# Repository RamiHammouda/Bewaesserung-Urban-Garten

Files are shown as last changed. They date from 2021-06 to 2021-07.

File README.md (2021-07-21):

# Bewaesserung Urban Garden

**HTW Smart Garden Watering System** is **_InternetOfThing_** **(IoT)**  **LoraWan** based Project from a wonderful suggestion of Mr. Prof. Dr.-Ing. Mohammad Abuosba. The target of the project is to build a smart watering system for an urban garden in HTW Berlin. 
<br/> <br/>
# Motivation
The ca.800m<sup>2</sup> Urban garden in HTW Berlin locates in the back of the university, next to the famous Spree River. It is a really beautiful garden which provides everyone fresh air along with really wonderful green feeling due to many trees and plants. And to have more time to enjoy it or to keep this feeling lasts forever, a smart watering system comes up as an answer :). 
<br/> <br/>
# Screenshot

 UI Program

# Usage

# Technology stack:
#### Operation System:
- Windows 10/(Linux)
#### IDE:
- Visual Studio Code
- Platform IO
#### Frameworks:
- Arduino
#### Dependencies:
- MCCI LoraWAN LMIC Library v4.4
- Adafruit Unified Sensor v1.1.4
- Adafruit BME280 v2.1.4
- Thingpulse/ESP8266 and ESP32 OLED driver for SSD1306 displays v4.2.0 (platformio lib install 2978)
- ~~NewPing v1.9.1~~ (replaced with our own implemented class)
#### Protocol:
- MQTT, HTTP
#### Connectivity Protocol:
- LoRaWAN (Long Range Wide Area Network)
#### Tools:
- MQTT Mosquito
- MQTT Explorer
- MQTT Fx
#### Server:
- TTN (thethingsnetwork)
#### UI Programming: 
- JavaScript
- Node-Red Framework
#### UI Dependencies:
- node-red-dashboard (base)
- node-red-contrib-ui-led (led only)
- node-red-contrib-telegrambot (connect to telegram bot API)
- node-red-contrib-remote (remote system on Mobile)
#### Hardware Programming: 
- C++
#### Hardware:
- Lora32 (TTGO-Lora v2.1.6)
+ BME280 Sensor
+ YF-S201 Waterflow sensor
+ Water pressure sensor 
+ HC-SR04 Ultrasonic sensor
+ Capacitive soil moisture sensor v1.2
+ Water pump
+ Magnetic Ventil
+ SRD-05VDC-SL-C 4 CH Relay
<br/> <br/>
# Feature List

##### Controlling Sensors, Actors:
- [x] Collect current ambient parameters (Temperatur sensor, Humidity sensor, Air pressure sensor.. )
- [x] Collect current water level in water tank (Ultrasound sensor)
- [x] Collect current water hose parameters (Water pressure sensor, Water flow sensor)
- [x] Control Actors (Water pump, Magnetic valve)
##### On LoraWan Server:
- [x] Send collected sensor data to TTN Network
- [x] Operate with ABP Mode or OTAA Mode (prefer OTAA)
- [x] Support float decode payload
- [x] Support int decode payload
- [x] Binding Server with opensensemap.org
##### Operate Actors:
- [x] Watering System can run independently of controlling UI
- [x] Actors can be manually remote-controlled 
- [x] Actors can operate itself automatically based on pre-configuration
     - [x] Watering will turn on if Moisture (Dryness) Value over a definied value (default is 95%)
     - [x] Watering will turn off if Moisture (Dryness) Value under a definied value (default is 90%)
     - [x] Watering will turn off if Water Level under a definied value (default is 10%)
     - [x] Watering will turn off if Waterflow Volume over a definied value (default is 10L for testing)(experiment feature)
- [x] Auto Mode and Manual Mode should be selectable (by Master Switch)
- [x] Remote control actors manually 
- [x] Updating-sensor Tempo is changeable (through Debug Mode on/off for quick/slow)
##### Sensor Data Visualization:
- [x] Simple sensor data are visualizated by opensensemap
- [x] Complex sensor data will be visualizated by a self development UI
##### UI Development:
- [x] Create an UI to get all current information of system ( Temperatur, Humidity, Moisture Value, Air Pressure, Water Pressure, Waterflow Speed, Waterflow Volume, current status of Ventil, current status of Pump, current Update Tempo, current operation status of system)
- [x] Assisten Management Information (Streng of Signal, Noise Ratio, relative Water Pressure, Curent Operation Mode )
- [x] Control actors through simple user-friendly UI like button, not on JSON UI 
      (comply to requirement from Mr. Prof. Dr.-Ing. Abuosba )
- [x] Pre-configuration parameters should be changeable (e.g through input fields) 
      (comply to suggestion from Mr. Holger Martin )
##### Options:
- [x] An UI on mobile for convenient monitoring
- [x] Send Notification to user for alert and notify current status automatically through Telegram with Bot "HTWGarden". (Only Admin received alert)
- [x] Everyone can query current important status of system through Telegram bot "HTWGarden"
- [x] Create wrapper classes for multiple sensors/actors (for an easy scalability)
 <br/> <br/>
## For testing purpose
#### THETHINGSNETWORK.ORG _(Legacy V2 Console)_
- ##### User name: _htwgardenproject_
- ##### Email address: _htwgardenss21@gmail.com_
- ##### Password: _htwgarden2021_

## UI Rebuild: (build from Flow.json file)
**Default:**
- **Logic base: _localhost:1880_**
- **UI board: _localhost:1880/ui_**
### MQTT Topic Setting:
- **MQTT-In Topic:**  **_mygardenproject/devices/sensortest02/up_**
- **MQTT-Out Topic:**  **_mygardenproject/devices/sensortest02/down_**
- **Server:**  **_eu.thethings.network_**
- **Port:**  **_1883_**
- **Protocol:**  **_MQTT V3.1.1_**
- **Username:**  **_mygardenproject_**
- **Password:**  **_ttn-account-v2.60jnFj-pF6rapK8BtiWsr2CQXM8TufQspWzjreeI2Zc_**
### Telegrambot:
- **Bot-Name: _HTWGarden_**
- **Token: _1565148953:AAHQ8Jx3c4r1mIf3uV5PS_4BW0aKDrDjfuM_**
 <br/> <br/>
# License
**MIT** © **HTW Berlin - IngenieurInformatik SS21** - **Team 4 - Khac Hoa Le, Rami Hammouda, Jaro Machnow**

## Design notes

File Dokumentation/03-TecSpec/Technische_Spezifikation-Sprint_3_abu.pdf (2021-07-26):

Technische Spezifikation - Smarte Gartenbewässerung

# Technische Spezifikation

# Smarte Gartenbewässerung über LoRaWAN

Mitarbeiter und Autoren:

- Rami Hammouda
- Khac Hoa Le
- Jaro Machnow

Letzte Änderung: 21.07.2021

Version: 1.5

21.07.2021 | Seite 1 von 39

## eine insgesamt sehr gute technische Spezifikation. Die Pin-Belegung im Schaltplan

sowie die Bemaßung des Gehäuses für den Ultraschallsensor fehlen.
weitere kleine Anmerkungen siehe unten.

## Wertung: TechSpec : 5 Punkte Projektplan : 5 Punkte

Technische Spezifikation - Smarte Gartenbewässerung

Inhaltsverzeichnis

1. Einleitung | 4
1.1 Überblick | 4
1.2 Definitionen und Abkürzungen | 4
1.3 Vorhandene Dokumente | 4
2. Prozessüberblick | 4
2.1 Realisierungsprozess | 5
2.2 Fachlicher Workflow | 7
2.3 Checkliste | 8
3. Systemarchitektur und Infrastruktur | 10
3.1 Systemarchitektur | 10
3.2 Beschreibung der Komponenten | 11
4. Technische Spezifikation der Software | 12
4.1 Überblick Software-Komponenten | 12
4.2 Schnittstellen zwischen den Komponenten | 14
4.3 Technologiestack | 15
4.4 Anmeldedaten für TTN | 16
4.5 Erste Testphase - Senden und Empfangen von Daten über TTN | 17
4.6 Entwicklung der User Interface (UI) | 23
4.7 Integration von Telegram | 25
4.8 Lora32-Komponente: Klassendiagramm | 26
4.9 Autonome Steuerung | 27
4.10 Fehlererkennung und -behandlung | 29
5. Spezifikation der Hardware | 30
5.1 Einzelteile | 30
5.2 Schaltplan | 35
5.3 Halterung für den Ultraschallsensor | 37
5.4 Gesamtaufbau | 39

Technische Spezifikation - Smarte Gartenbewässerung

Versionshistorie

Version | Datum | Verantwortlich | Änderung
1.0 | 29.05.2021 | Jaro Machnow | Dokumenterstellung
1.1 | 06.06.2021 | Jaro, Hoa Le, Rami | Ergänzungen
1.2 | 15.06.2021 | Jaro, Hoa Le, Rami | Ergänzungen
1.3 | 16.06.2021 | Rami, Hoa, Jaro | Vervollständigung Sprint 1
1.4 | 15.07.2021 | Jaro, Hoa Le, Rami | Ergänzungen
1.5 | 21.07.2021 | Jaro, Hoa Le, Rami | Vervollständigungen Sprint 3

Technische Spezifikation - Smarte Gartenbewässerung

### 1. Einleitung

### 1.1 Überblick

Es wird eine smarte und möglichst preisgünstige und überwachte Bewässerung von Beeten per Netzwerksteuerung über das The-Things-Network (TTN) gebaut. Im Urban Garden kontrolliert ein Mikrocontroller entsprechend der über das Netzwerk gesendeten Nutzereingaben oder eines autonomen Workflows verschiedene Sensoren und Aktoren. Mit Hilfe einer LoRaWAN-Antenne werden die Daten der Sensoren vom Urban Garden aus in das Netzwerk gesendet und können auf einem entfernten Computer ausgelesen werden und als Visualisierung auf OpenSenseMap.org angesehen werden.

Zu den Mechanismen der autonomen Steuerung gehören vor allem das Abschalten des Wasserflusses im Falle eines Lecks und das eigenständige Starten der Bewässerung beim Erreichen einer bestimmten Bodenfeuchte.

Für alle eingebauten Komponenten und Funktionen gilt der Grundsatz, dass das System in Zukunft leicht modular erweitert werden kann.

### 1.2 Definitionen und Abkürzungen

LoRaWan -Long Range Wide Area Network TTN - The Things Network

### 1.3 Vorhandene Dokumente

Tabelle 1: Vohandene Dokumente

Dokument | Autor(en) | Datum
Lastenheft | Rami Hammouda, Khac Hoa Le, Jaro Machnow | 28.04.2021
Lastenheft + Kommentare | + Prof. Dr. Mohammad Abuosba | 30.04.2021
Anforderung-Email | Holger Martin | 10.04.2021
Pflichtenheft | Rami Hammouda, Khac Hoa Le, Jaro Machnow | 19.05.2021
Pflichtenheft + Kommentare | + Prof. Dr. Mohammad Abuosba | 25.05.2021

Technische Spezifikation - Smarte Gartenbewässerung

### 2. Prozessüberblick

### 2.1 Realisierungsprozess

Nachfolgend ist eine Darstellung aller Funktionen und deren Unterteilung im Projekt:

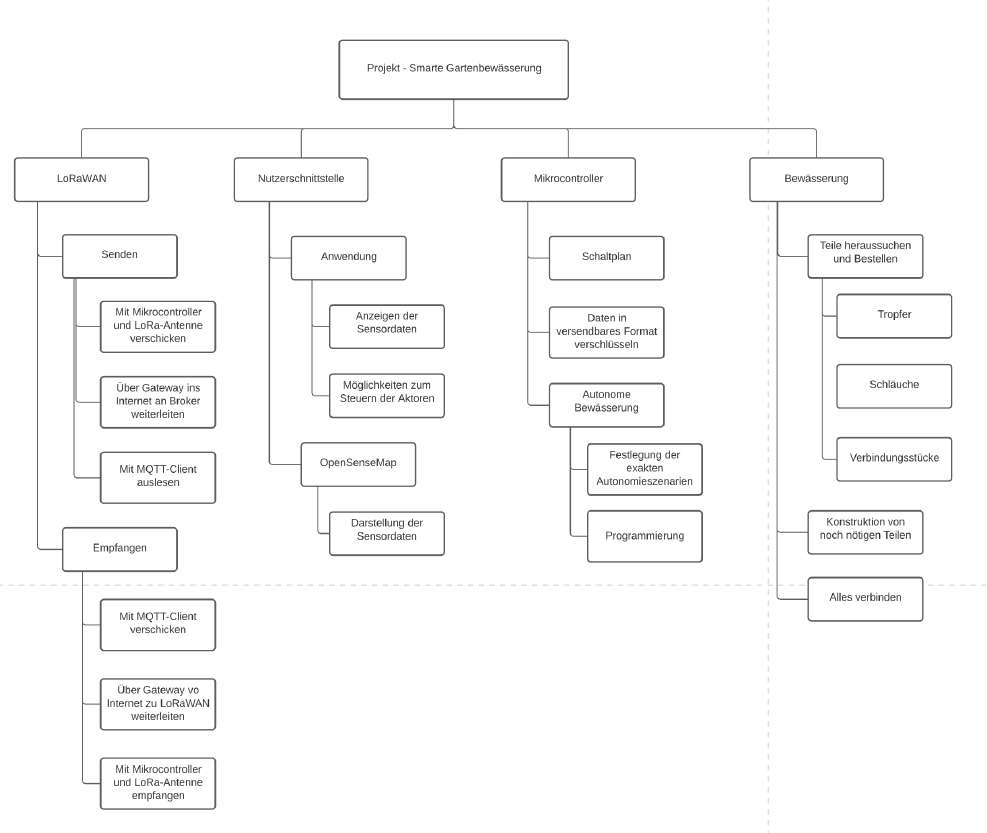
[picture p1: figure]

Abbildung 1: Übersicht über die Aufgabenstruktur

Für die Realisierung des Projektes ist es zuerst nötig, alle notwendigen Teile herauszusuchen und zu bestellen. Dann kann damit begonnen werden die Funktionsfähigkeit des Hauptziels des Projektes sicherzustellen: Das Senden und Empfangen von Daten vom Urban Garden über das LoRaWAN-Netzwerk. Danach können parallel die Nutzerschnittstellen mit TTN verbunden und programmiert werden und der Mikrocontroller mit den zugehörigen

Technische Spezifikation - Smarte Gartenbewässerung

Komponenten eingerichtet werden. Zum Schluss wird das gesamte Bewässerungssystem mit allen Komponenten zusammengebaut und im Urban Garden installiert.
Der Realisierungsprozess ist in folgendem Diagramm dargestellt:

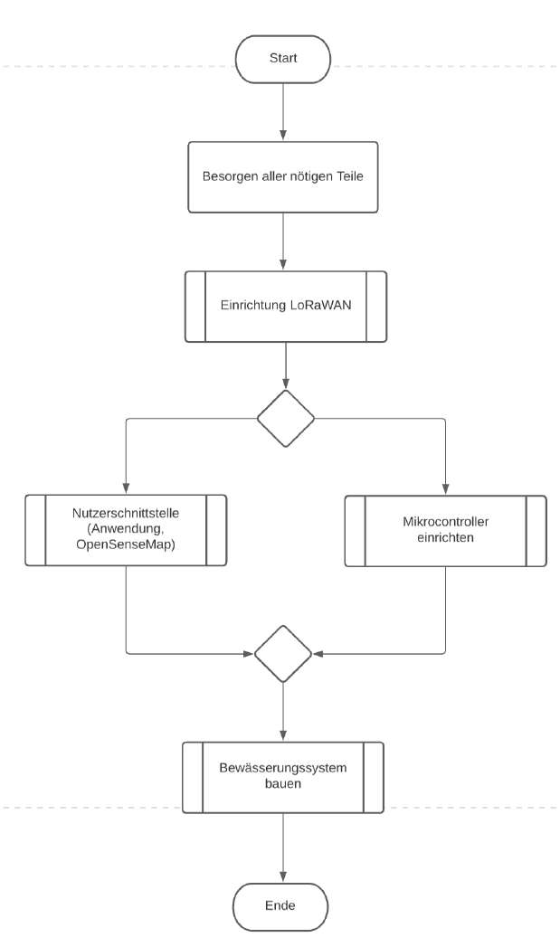
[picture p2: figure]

Abbildung 2: Diagramm des Realisisierungsprozesses

Technische Spezifikation - Smarte Gartenbewässerung

### 2.2 Fachlicher Workflow

Nachfolgen ist das Diagramm des fachlichen Workflows zu sehen. Hier kann die Zusammenarbeit der Software und Hardware gesehen werden und der Ablauf bei Benutzung, Überwachung und Steuerung des Systems.

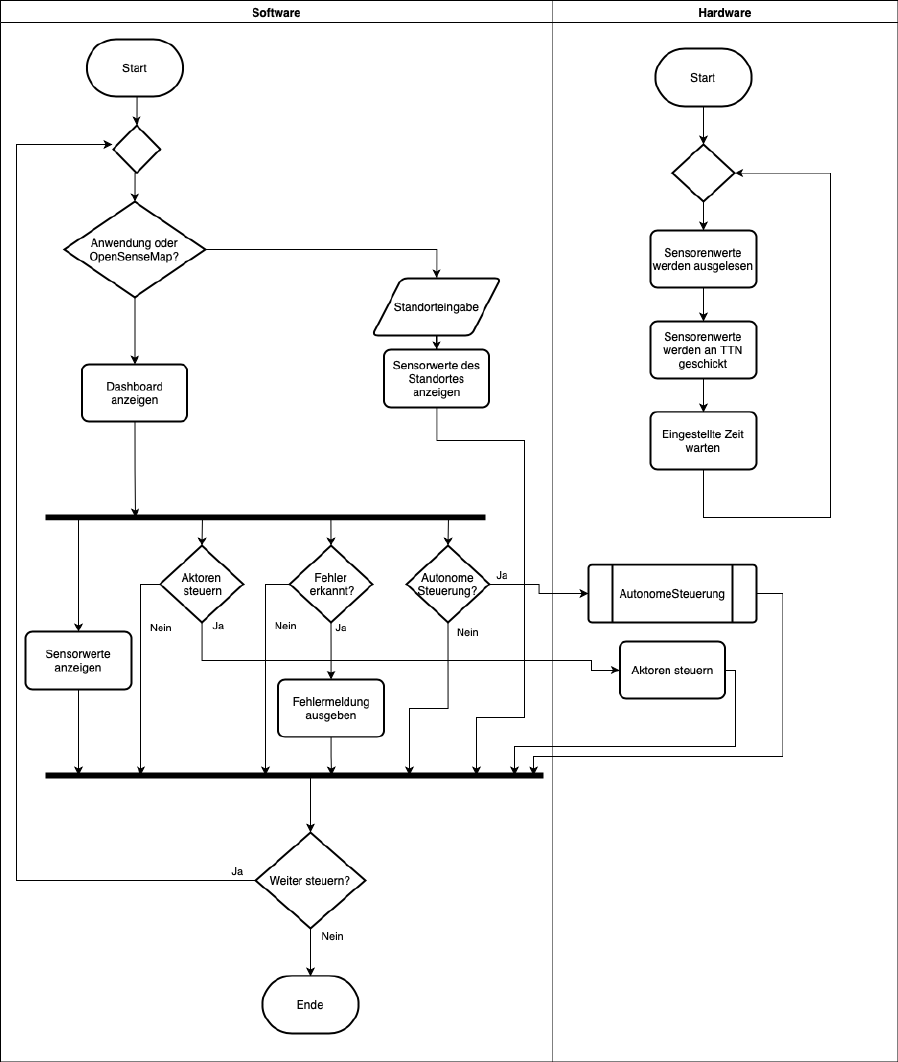
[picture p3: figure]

Abbildung 3: Fachlicher Workflow

Technische Spezifikation - Smarte Gartenbewässerung

### 2.3 Checkliste

Zur Strukturierung unserer Arbeit und um zu wissen, was schon gemacht wurde und was noch zu erledigen ist, haben wir folgende Checkliste erstellt. Die Checkliste beinhaltet aktuell nur Punkte, die mit der Software im Zusammenhang stehen (für den 1. Sprint).

Controlling Sensors, Actors:

Collect current ambient parameters (Temperatur sensor, Humidity sensor, Air pressure sensor.. )
Collect current water level in water tank (Ultrasound sensor)
Collect current water hose parameters (Water pressure sensor, Water flow sensor) Control Actors (Water pump, Magnetic valve)

On LoraWan Server:

Send collected sensor data to TTN Network
Operate with ABP Mode or OTAA Mode (prefer OTAA) Support float decode payload
Support int decode payload
Binding Server with opensensemap.org

Operate Actors:

Remote control actors manually
Actors operates itself automatically based on pre-configuration Auto Mode and Manual Mode should be selectable

Sensor Data Visualization:

Simple sensor data are visualizated by opensensemap
Complex sensor data will be visualizated by a self development UI

Technische Spezifikation - Smarte Gartenbewässerung

UI Development:

Create a UI to get all current information of system
Control actors through simple user-friendly UI like button, not on JSON UI (comply to requirement from Mr. Prof. Dr.-Ing. Abuosba )
Pre-configuration parameters should be changeable (e.g through input fields) (comply to suggestion from Mr. Holger Martin )

Options:

An UI on mobile for convenient monitoring Send Notification to user for alert

Technische Spezifikation - Smarte Gartenbewässerung

### 3. Systemarchitektur und Infrastruktur

### 3.1 Systemarchitektur

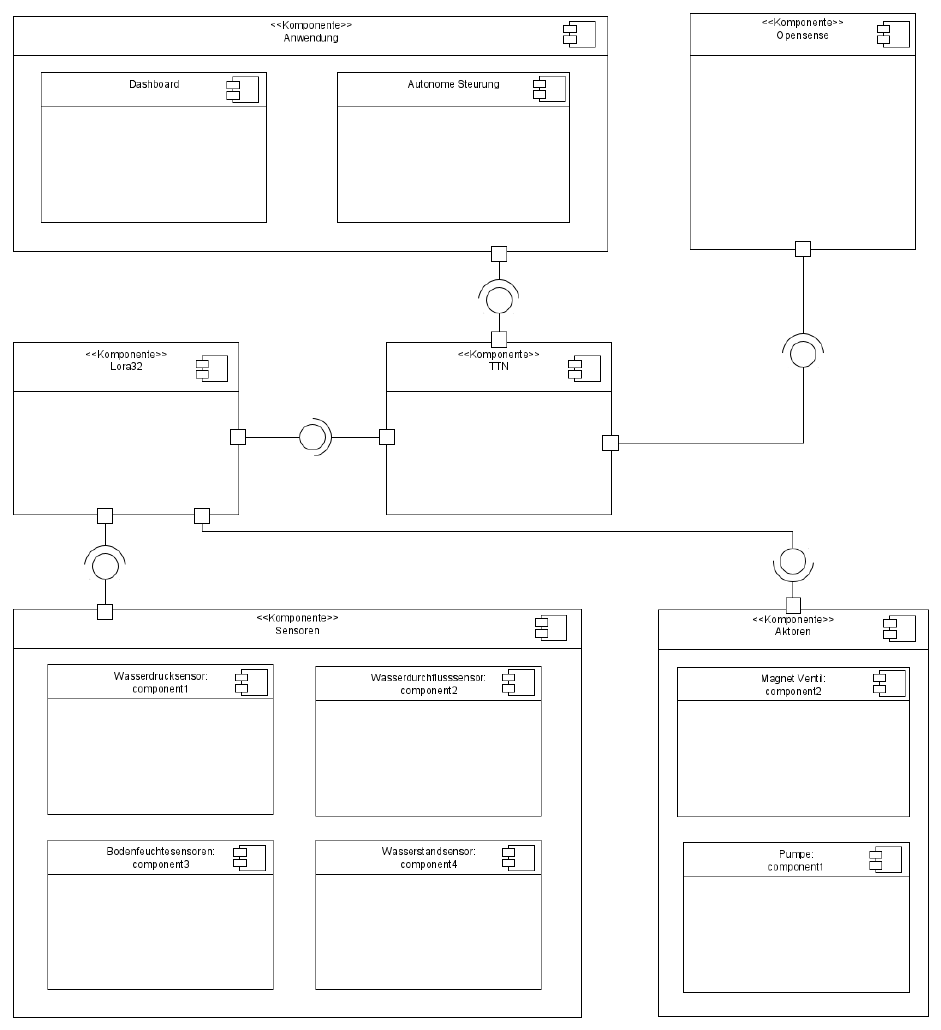
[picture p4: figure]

Abbildung 4: Komponentendiagramm

Technische Spezifikation - Smarte Gartenbewässerung

### 3.2 Beschreibung der Komponenten

Das Komponentendiagramm zeigt die verschiedenen Schichten des Bewässerungssystems:
- Ganz oben sind die Komponenten, mit denen der Nutzer interagieren kann. Dazu gehören die Anwendung und die OpenSenseMap. Bei der Anwendung sieht der Nutzer das Dashboard, in dem Sensordaten angezeigt werden können und Aktoren per Knopfdruck aktiviert oder deaktiviert werden können. Zudem kann die autonome Steuerung aktiviert werden. Die OpenSenseMap zeigt eine Karte und die Sensordaten für den Standort des Urban Gardens.
- In der Mitte befinden sich Komponenten, die die obere Anwendungsschicht mit den Sensoren und Aktoren im Urban Garden verbinden. Dazu gehören das TheThingsNetwork und der Lora32-Mikrocontroller. Über diese beiden Daten kommen die Sensordaten zur Nutzeranwendung und die Nutzereingaben zu den Aktoren. Die Kommunikation bzw. Übertragung der Daten erfolgt hier über das LoRaWan-Netzwerk und über das Internet. Nähere Informationen sind dazu in Punkt 4.2 nachzulesen.
- Unten befinden sich die Komponenten, die direkt im Urban Garden agieren, also alle Sensoren und Akoren. Dazu gehören: Wasserdrucksensor, Wasserdurchflusssensor, Wasserstandsensor, Bodenfeuchtigkeitssensor, Pumpe und Magnetventil. Diese Komponenten sind mit Lora32 verbunden und werden dadurch überwacht und gesteuert.

Technische Spezifikation - Smarte Gartenbewässerung

### 4. Technische Spezifikation der Software

### 4.1 Überblick Software-Komponenten

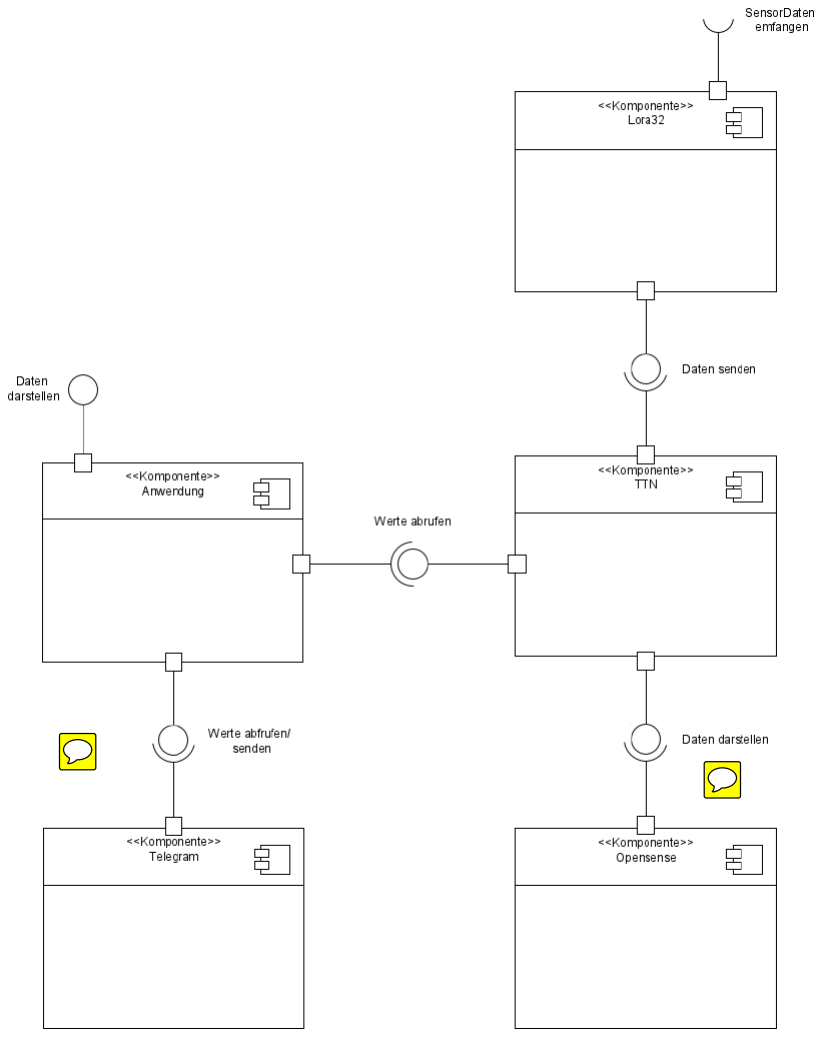
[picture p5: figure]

Abbildung 5: Komponentendiagramm Software

Technische Spezifikation - Smarte Gartenbewässerung

Beschreibung der Software-Komponenten:

Tabelle 2: Software-Komponenten

SW Komponente | Funktionen | Sprache/Typ
Anwendung (geplant) | -Daten empfangen und anzeigen - Daten auswerten - Daten senden - Alles wird in einem Dashboard angezeigt | JavaScript (Node Js)
Opensensemap (geplant) | -Anzeigen der Messdaten auf einer Karte | Website Service als Client
Telegram (geplant) | -Schnell und aktuell die Daten und den Status vom System abrufen | API Service als Client
Lora32 (Software) | -Sensorendaten abrufen - Aktoren steuern - Signal schicken/empfangen. | Programming language C++
TTN | -Zentraler Server für LoRaWAN - Schnittstelle zwischen LoRaWAN und Client. - Datenbank: Automatische Speicherung der Daten einer Woche | Website Server

Technische Spezifikation - Smarte Gartenbewässerung

### 4.2 Schnittstellen zwischen den Komponenten

Die Datenübermittlung zwischen dem LoRa32-Mikrocontroller und der Anwendung erfolgt in mehreren Schritten:
1. LoRa32 sendet die Daten an TTN-Gateways mit Hilfe der LoRaWan-Antenne.
2. Das Gateway schickt die Daten weiter ins Internet an die TTN-Cloud durch HTTP.
3. Die Anwendung ist mit der TTN-Cloud verbunden und erhält so die Daten.

Die TTN-Cloud dient dabei zugleich als Datenbank und speichert automatische die Daten einer Woche. Die Anwendung dient als grafische Benutzeroberfläche, die es dem Nutzer ermöglicht die Daten aus dem System auszulesen und das System fernzusteuern. Umgekehrt, also von der Anwendung zum LoRa32, funktioniert der Vorgang analog:
1. Der Nutzer gibt Daten in der Anwendung ein. Die Daten werden an die TTN-Cloud übermittelt.
2. Die TTN-Cloud übermittelt die Daten über HTTP an das TTN-Gateway
3. Mit Hilfe der LoRaWan-Antenne werden die Daten vom Gateway an den LoRa32-Mikrocontroller gesendet.
Die OpenSenseMap auch mit der TTN-Cloud verknüpft, um Daten anzuzeigen. Das funktioniert auf die gleiche Weise, wie bei der Anwendung. OpenSenseMap dient als weitere Benutzerschnittstelle.
Zudem wird Telegram benutzt, um eine schnelle und unkomplizierte Kommunikation des Nutzers mit dem System zu ermöglichen. Telegram ist direkt mit der Anwendung verknüpft.

Technische Spezifikation - Smarte Gartenbewässerung

### 4.3 Technologiestack

Folgender Technologiestack wird für die Erstellung der Software für die Kommunikatin über LoRaWan verwendet:

Tabelle 3: Technologiestack

Operation System: | -Windows 10/(Linux)
IDE: | -Visual Studio Code - Platform IO
Framework: | -Arduino
Abhängigkeiten: | -MCCI LoraWAN LMIC Library v3.3 - Adafruit Unified Sensor v1.1.4 - DHT sensor library v1.4.2
Protokolle: | -MQTT - HTTP
Drahtlose Verbindung/ Kommunikation: | - LoRaWAN (Long Range Wide Area Network)
Tools: | -MQTT Mosquito - MQTT Explorer
Server: | -TTN (thethingsnetwork)
UI Programmierung: | -JavaScript - NodeJS
Hardware Programmierung: | -C++
Hardware: | -Lora32 (TTGO)

Technische Spezifikation - Smarte Gartenbewässerung

### 4.4 Anmeldedaten für TTN

Mit folgenden Daten kann man sich beim TTN-Account unseres Teams anmelden, Einstellungen vornehmen und empfangene Sensordaten einsehen und Aktoren steuern:

THETHINGSNETWORK.ORG (Legacy V2 Console)
User name: htwgardenproject
Email address: htwgardenss21@gmail.com Password: htwgarden2021

Technische Spezifikation - Smarte Gartenbewässerung

### 4.5 Erste Testphase - Senden und Empfangen von Daten über TTN

Bevor die Verbindung der TTN-Server mit der Anwendung, OpenSenseMap und Telegram erstellt wird, wird zunächst die Kommunikation über LoRaWan mit MQTT-Mosquito, MQTT.Fx und MQTT-Explorer getestet.
Wenn die Daten von LoRa32 sicher erzeugt werden, wird LoRa32 mit dem TTN-Server verbunden. Bei der TTN-Cloud können Uplinks (Signal von Sensoren) gelesen werden und die Downlinks (Signal zur Sensoren) geschickt werden. Das Emfpangen von Sensordaten und das Schicken von Daten zur Steuerung von Aktoren werden getestet.
In der Testschaltung werden die Daten des DHT22 Temperatur- und Luftfeuchtigkeitssensors vom Lora32 erfasst. Dann werden die Daten weiter an TNN gesendet. Bei jedem Senden leuchtet die grüne LED. Zusätzlich kann ein Signal von TTN aus gesendet werden um die rote LED an- bzw. auszuschalten.
Bei dem ersten Test stand uns ein Lora32 v1 zur Verfügung. Ein Bild dieser Schaltung ist in nachfolgender Abbildung zu sehen:

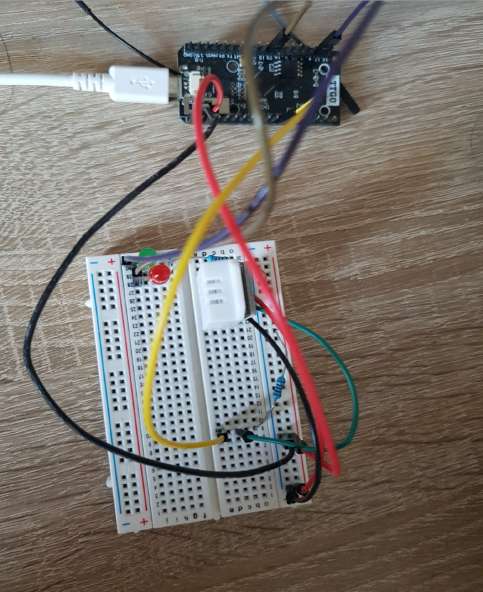
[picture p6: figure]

Abbildung 6: Aufbau der Schaltung für den Test der LoRaWan-Verbindung (Lora32 V1 ohn Oled)

Technische Spezifikation - Smarte Gartenbewässerung

Wenig später stand die neuere Version des TTGO Lora32 zur Verfügung: Lora32 OLED V2.1.6. Auf dem Display werden direkt die gemessenen Sensordaten angezeigt. So kann geprüft werden, ob die Daten korrekt an TTN übertragen werden und gleiche Werte angezeigt werden.

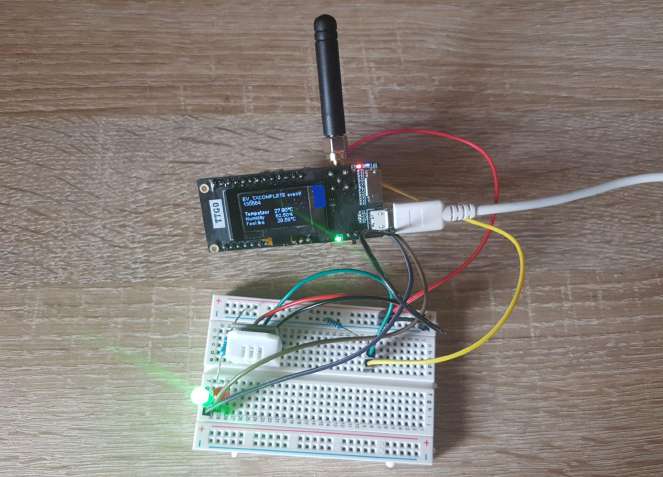
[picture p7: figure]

Abbildung7: Aufbau der Schaltung für den Test der LoRaWan-Verbindung (Lora32 OLED V2.1.6)

In Gitlab → Software → Node-Lora32 → src → main.cpp ist der C++ Code zu finden, der auf

dem Lora32 installiert ist. Grundlegend gibt es eine Funktion zum Auslesen der Sensordaten des DHT22, zum Steuern von einer grünen und einer roten LED, zur Umwandlung der Daten in Byte mit dem Encoder, um sie versenden zu können und zum Senden der Daten über die Lora-Antenne.
Die Daten werden von einem TTN-Gateway empfangen und ins TTN-Netzwerk zu einem TTN-Server weitergeleitet. Mit dem Tool MQTT-Mosquitto oder MQTT-Explorer oder mit der Website von von TTN können wir auf die Daten in TNN zugreifen und die Sensordaten auslesen.

Technische Spezifikation - Smarte Gartenbewässerung

1. MQTT-Mosquito (als Client betrachtet)
Folgende Daten werden zur Verbindung über MQTT benötigt (um auf die Daten auf dem Daten TTN-Server zuzugreifen):
App ID on TTN: mygardenproject
Access key on TTN: ttn-account-v2.60jnFj-pF6rapK8BtiWsr2CQXM8TufQspWzjreeI2Zc

Folgende Befehle müssen in die Konsole eingegeben werden :
Active Mosquito service:
net start mosquitto
Subscribe our topic:
mosquitto_sub -h eu.thethings.network -p 1883 -d -u mygardenproject -P ttn-account-v2.60jnFj-pF6rapK8BtiWsr2CQXM8TufQspWzjreeI2Zc -t #

In nachfolgendem Bild sieht man die Ausgabe in der CMD ür MQTT-Mosquitto.

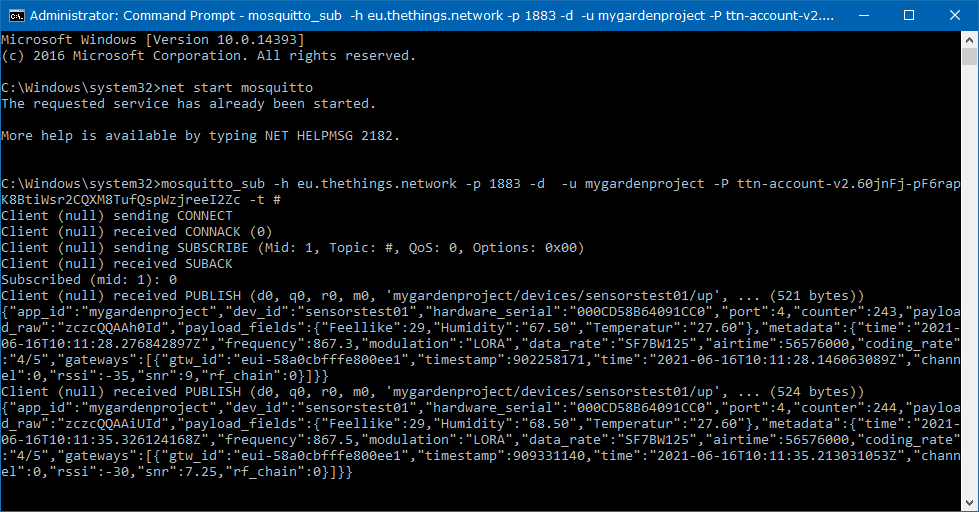
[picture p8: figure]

Abbildung 8: MQTT Mosquito

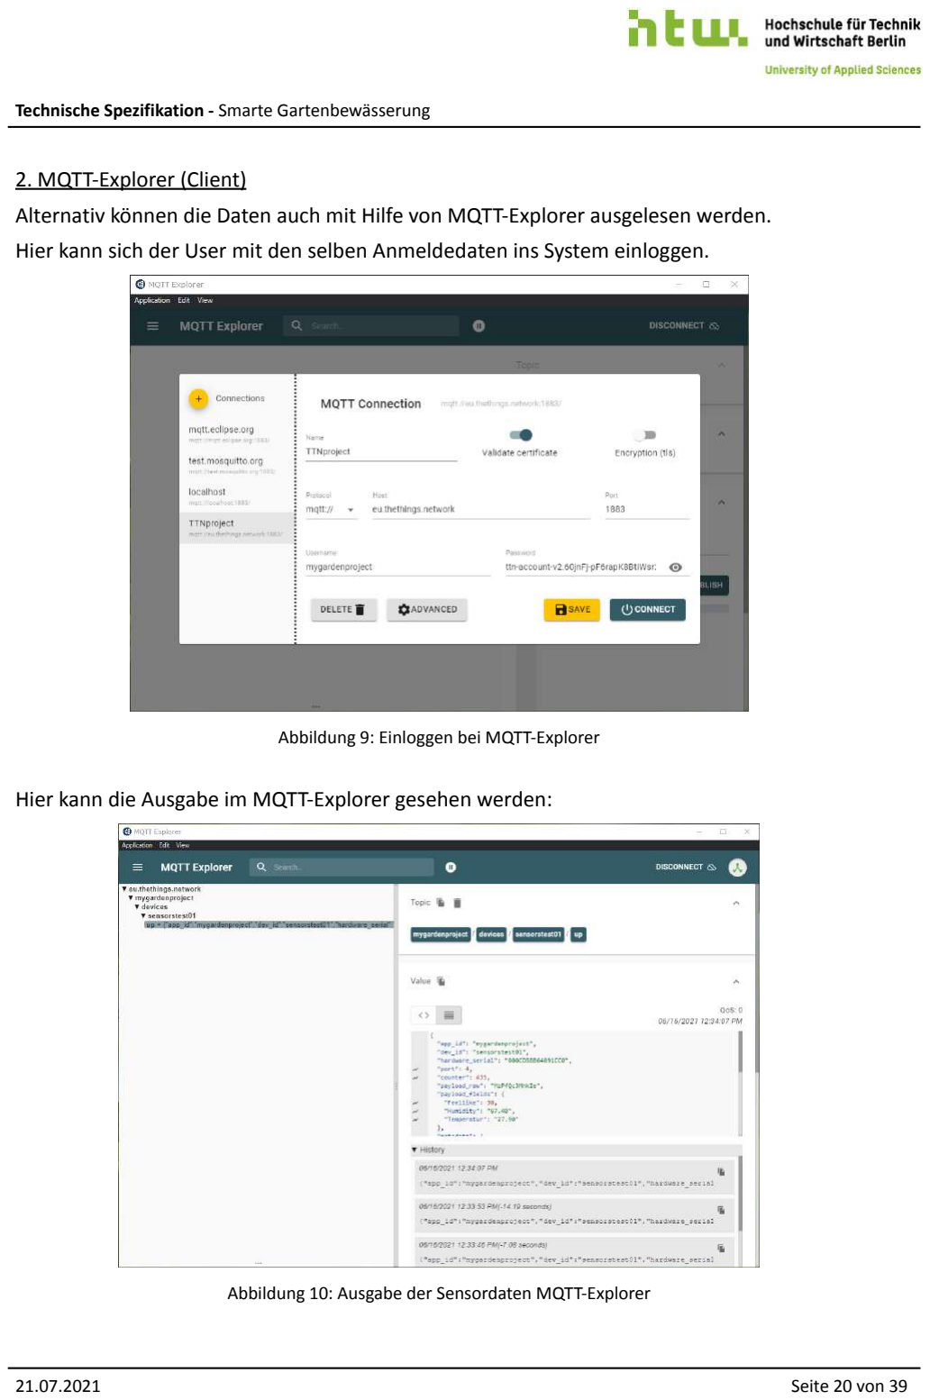
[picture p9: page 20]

Technische Spezifikation - Smarte Gartenbewässerung

2. MQTT-Explorer (Client)
Alternativ können die Daten auch mit Hilfe von MQTT-Explorer ausgelesen werden. Hier kann sich der User mit den selben Anmeldedaten ins System einloggen.

Abbildung 9: Einloggen bei MQTT-Explorer

Hier kann die Ausgabe im MQTT-Explorer gesehen werden:

Abbildung 10: Ausgabe der Sensordaten MQTT-Explorer

Technische Spezifikation - Smarte Gartenbewässerung

3. TTN-Website (Server + Client)
Die schönste und einfachste Möglichkeit, um die Daten auszulesen, ist das direkte Nutzen der Website von TTN.
Um die Daten dekodieren zu können, muss zuerst das Payload-Format auf der Website von TTN geschrieben werden, um die empfangenen Daten von Byte zurück in ein lesbares Format umzuwandeln.
In folgendem Bild ist die Funktion zum Dekodieren zu sehen:

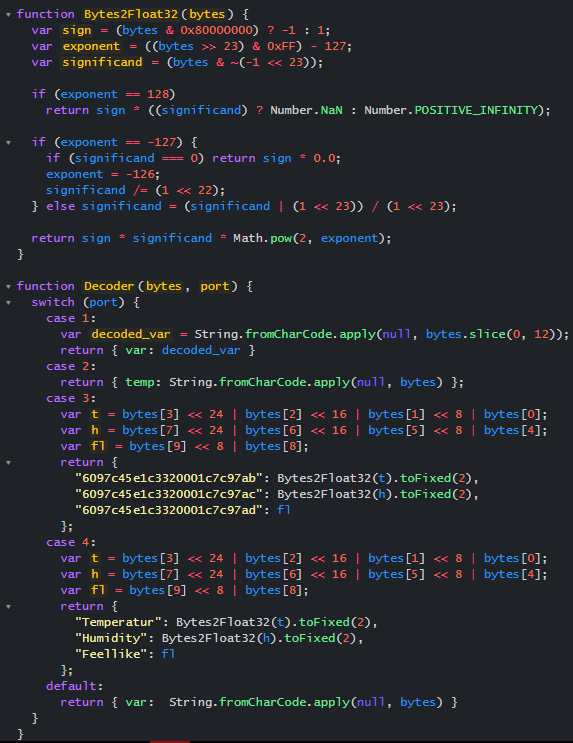
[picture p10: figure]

Abbildung 11: Payload-Dekodier-Code

Technische Spezifikation - Smarte Gartenbewässerung

Dann können die Daten bei TTN gelesen werden:

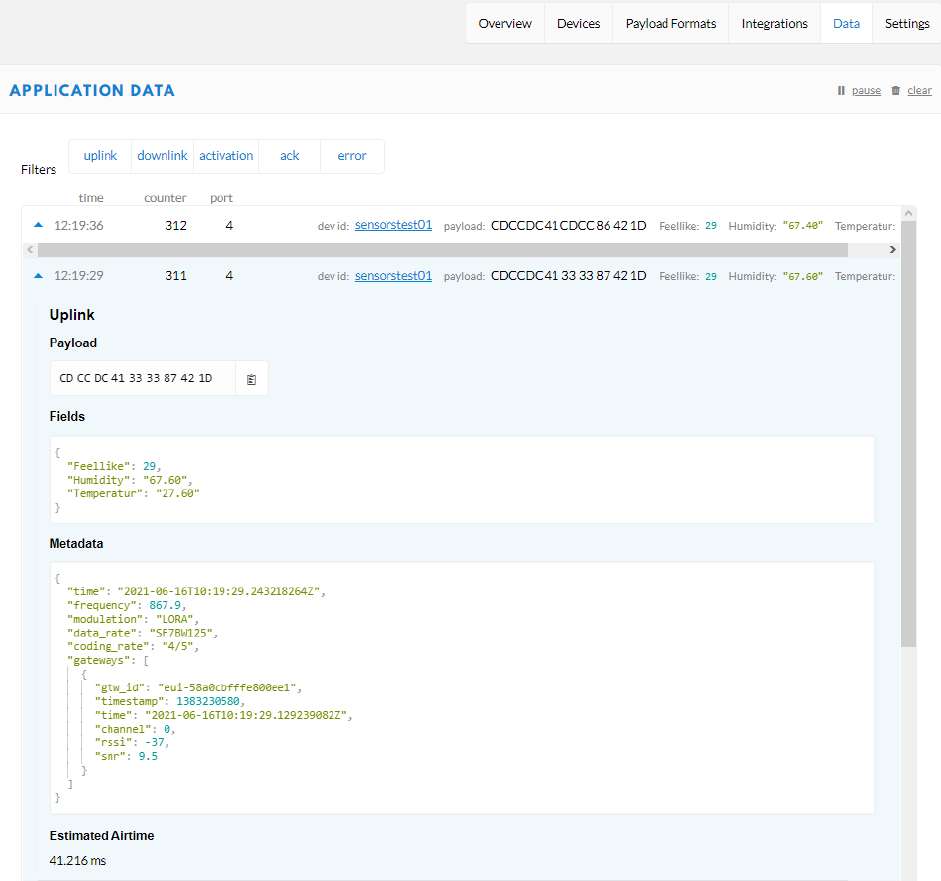
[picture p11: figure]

Abbildung 12: Datenausgabe TNN

Technische Spezifikation - Smarte Gartenbewässerung

### 4.6 Entwicklung der User Interface (UI)

Entsprechend der ersten Testphase, in der in der Testschaltung ein DHT22 Temperatur- und Luftfeuchtigkeitssensor und zwei LEDs verbaut waren, wurde ein User Interface erstellt, das folgende Funktionen hat:
- Zahlenwerte der aktuellen Sensordaten (Temperatur, Luftfeuchtigkeit, Feel-Like-Temperatur)
- Verlaufsdiagramme für diese Sensorwerte
- Schalter für den Wechsel zwischen Auto und Manual Mode
- Schalter für das Aktivieren/Deaktivieren des Aktors (LED) im Manual Mode
- Hinweis-Leuchte, die grün leuchtet, sobald ein Signal über TTN empfangen wird
- Diagramme für Signal Noise und Signal Strength (Werte sind gut, wenn: Signal Noise zwischen -20 dB bis 10 dB und Signal Strength zwischen -120 dBm bis -30 dBm) Das User-Interface wurde mit Node-Red entwickelt und mit TTN über eine Schnittstelle verbunden.
Nachfolgend ist das User Interface zu sehen:

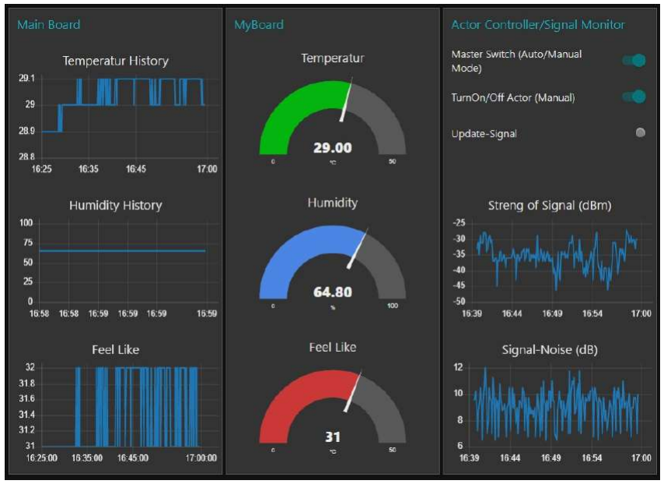
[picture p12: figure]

Abbildung 13: Erstes Test-UI

Technische Spezifikation - Smarte Gartenbewässerung

Nachdem das System mit den richtigen Sensoren und Aktoren erweitert wurde, musste auch das User Interface erweitert werden.
Nachfolgende Informationen bzw. Aktionen können im finalen User Interface gesehen und benutzt werden:
- Gauge: Aktuelle Werte der Sensoren, die einen Minimal- und Maximalwert haben. (Temperatur, LuftFeuchtigkeit, Bodentrockenheit, Luftdruck, Wasserdruck, Druck in Leitung und Wasserstand)
- Histogram: Verlauf der Sensordaten, um einen zeitlichen Überblick zu erhalten. (Temperatur, Luftfeuchtigkeit, Bodentrockenheit, Wasserdruck, Wasserstand, Wasserdurchfluss-Geschwindigkeit, Strength of Signal und Signal Noise)
- Text: Aktuelle Werte von Sensoren, deren Werte kein Maximum haben (Wasserdurchfluss Geschwindigkeit, Wasserdurchfluss Volumen)
- LED: visualisiert den aktuellen Status von Aktor und den Update-Status: (Update-Signal, Ventil und Pumpe Status)
- Switch/Schalter: Wechsel zwischen verschiedenen Modi /Zuständen
(Manuell oder Auto Modus, Turn On/Off Watering System in Manual Mode und Debug Mode)
- Slider: Steuerungswerte, die zum autonomen Betrieb vom System gehören. (Bodenfeuchtigkeit zu an/aus, Wasserstand zu aus, Wasservolumen zu aus)

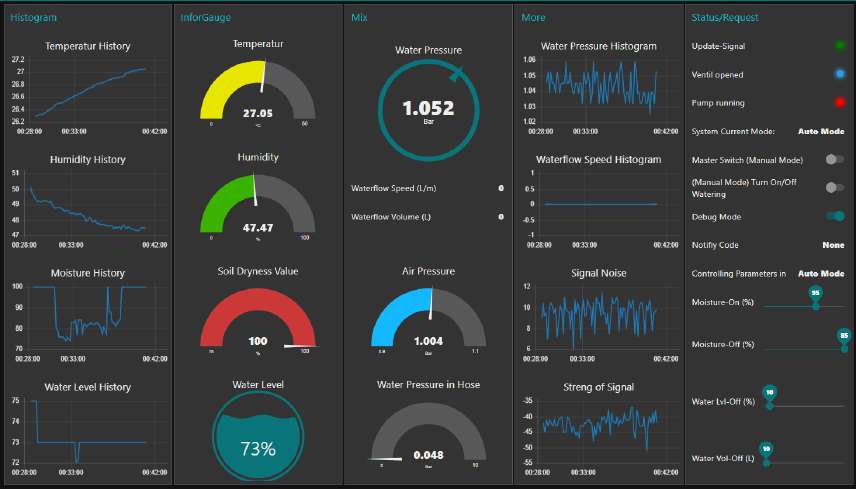
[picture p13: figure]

Abbildung 14: Finales UI

Technische Spezifikation - Smarte Gartenbewässerung

### 4.7 Integration von Telegram

Um eine weitere und sehr einfache Möglichkeit für den Nutzer bereitzustellen, um die Sensorwerte auszulesen. Deswegen wurde unser System mit Hilfe der Telegram Bot API mit dem Telegram-Messenger verbunden.
Der Nutzer kann somit schnell wichtige Informationen über aktuell Stand von Garten abfragen. Der Admin bekommt zudem jedes mal eine Nachricht, wenn die Bewässerung aktiviert oder deaktiviert wurde.
Nachfolgend sind Screenshots aus der Telegram-App auf einem Android-Smartphone.

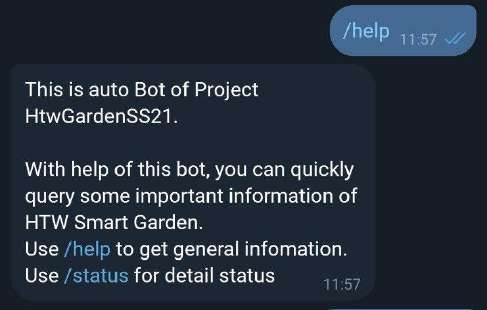
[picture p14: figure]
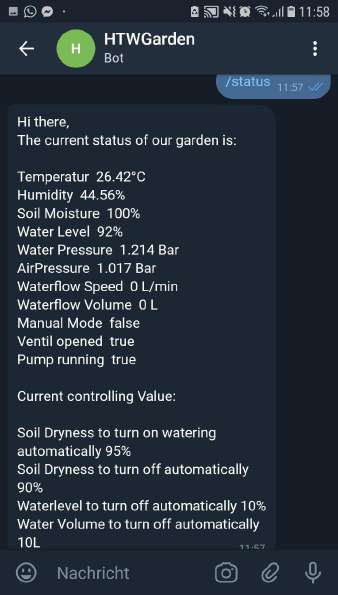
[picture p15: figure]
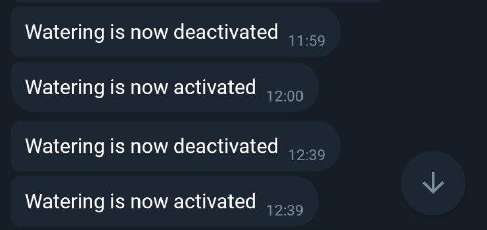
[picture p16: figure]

Abbildung 15: Screenshots von Telegram

Daten:
Telegram bot: HTWGarden (nicht HTW GardenSS21, da ist die alte Version)

Befehle:
- /help: allgemeine Informationen und Hinweise
- /status: aktuellen Stand vom Garten abfragen

Technische Spezifikation - Smarte Gartenbewässerung

### 4.8 Lora32-Komponente: Klassendiagramm

Um das System Modular zu gestalten und es einfach zu machen später neue Sensoren und Aktoren hinzuzufügen, wurde folgende Klassenhierachie für die Komponenten, die an den Lora32 angeschlossen werden, definiert:

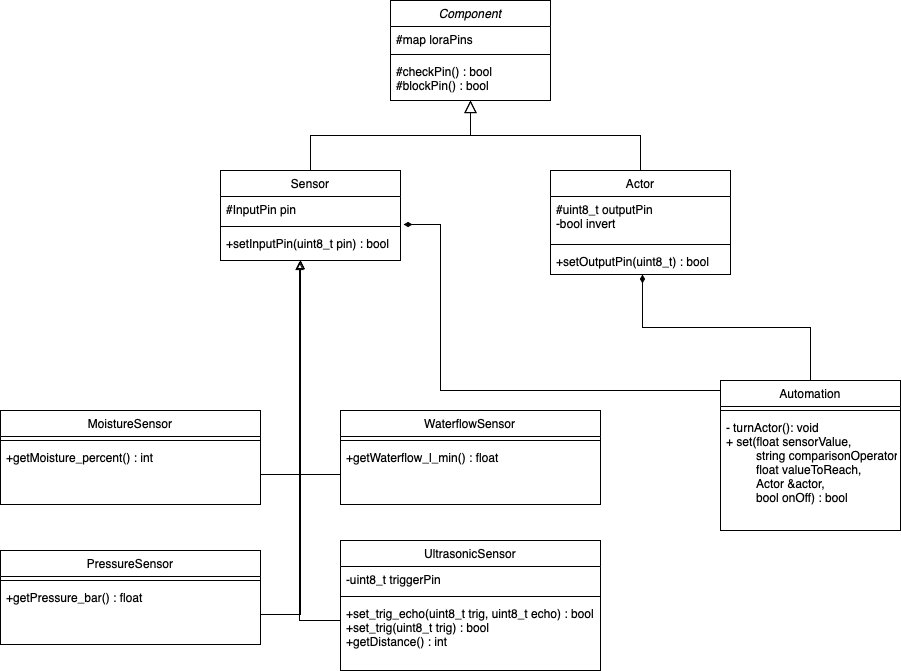
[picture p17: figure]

Abbildung 16: Klassendiagramm

Die Klassen Actor und Sensor erben von der Klasse Component. In der Klasse Component werden die Pins am Lora32 verwaltet:
- wird ein Sensor oder Aktor mit einem Pin registriert, kann dieser nicht nochmal verwendet werden
- es können nur Pins verwendet werden, die der Lora32 überhaupt hat

Technische Spezifikation - Smarte Gartenbewässerung

Von der Klasse Sensor erben die verwendeten Sensoren. Diese sind in einzelnen Klassen, da die Werte von jedem Sensor auf unterschiedliche Art und Weise ausgelesen werden müssen (analog, digital, interrupt).
Die Aktoren agieren alle gleich: man kann sie ein- oder ausschalten. Allerdings gibt es unterschiedliche Relais-Arten. Deswegen muss noch der bool-Wert “invert” hinzugefügt werden. Unser Relais schaltet in den Zustand “ein”, wenn kein Signal anliegt. Das Signal muss also dementsprechend invertiert werden.
Zusätzlich gibt es noch eine Klasse Automation, die in der Set-Funktion einen Ist-Sensor-Wert, einen Operator als string, einen Soll-Sensor-Wert, den Actor und einen bool, ob der Aktor aktiviert oder deaktiviert werden soll, entgegen nimmt. Wird die Funktion aufgerufen, werden die Werte entsprechend dem Operator verglichen und der Aktor aktiviert oder deaktiviert.

### 4.9 Autonome Steuerung

Unser System kann autonom und ganz unabhängig von der Verbindung mit TTN und damit auch von Eingaben des Nutzers betrieben werden.
Dazu muss der Nutzer einen Schalter (Master-Switch) umlegen, um die autonome Steuerung zu aktivieren. Diese Information wird dann an den Mikrocontroller gesendet, woraufhin dieser unabhängig von LoraWan die Bewässerung steuern kann.
Ist der autonome Modus aktiviert, können Parameter für die autonome Steuerung mit vier Slidern eingestellt werden:
- Moisture-On: ab welchem Trockenheitswert soll die Bewässerung aktiviert werden
- Moisture-Off: unter welchem Trockenheitswert soll die Bewässerung deaktiviert werden
- Water Lvl-Off: unter welchem Wasserstandswert soll die Bewässerung deaktivert werden
- Water Vol-Off: ab welchem Wert für das durchgeflossene Wasser soll die Bewässerung deaktiviert werden

Hinweis: Water Vol-Off funktioniert mit Hilfe von FreeRTOS (Free Real Time Operating System) möglich und bis jetzt nur ein experimentelles Feature. Nachdem der eingestellte

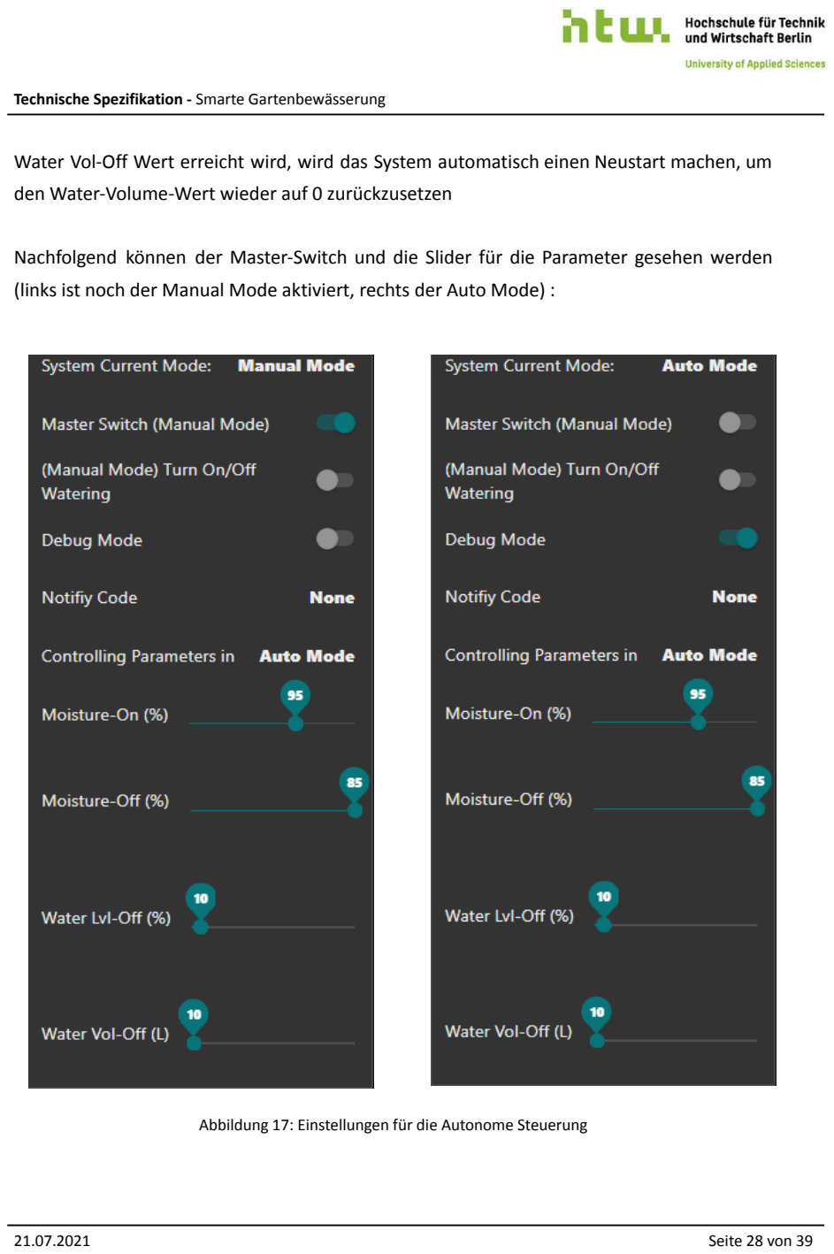
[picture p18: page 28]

Technische Spezifikation - Smarte Gartenbewässerung

Water Vol-Off Wert erreicht wird, wird das System automatisch einen Neustart machen, um den Water-Volume-Wert wieder auf 0 zurückzusetzen

Nachfolgend können der Master-Switch und die Slider für die Parameter gesehen werden (links ist noch der Manual Mode aktiviert, rechts der Auto Mode) :

Abbildung 17: Einstellungen für die Autonome Steuerung

Technische Spezifikation - Smarte Gartenbewässerung

### 4.10 Fehlererkennung und -behandlung

Das System hat die Fähigkeit, selbst Fehler zu erkennen und die Bewässerung dann automatisch zu deaktivieren, um kein Wasser zu verschwenden und Schäden zu vermeiden. Es sind zwei Fehlerszenarien definiert:
1. Druck in der Leitung sinkt unter 1 bar (wahrscheinlich Leck oder defekte Pumpe)
2. Druck in der Leitung steigt über 5,5 bar (wahrscheinlich Verstopfung)

Die voreingestellten Werte von 1 bar und 5,5 bar sind nur zur Simulation und müssen nach dem kompletten Aufbau (mit allen Schläuchen, Verbindungsstücken und Tropfern bzw. Regnern und weiteren Teilen) neu ermittelt werden, da sich dadurch die Vorbedingungen für die Standard-Werte im System ändern.
In nachfolgender Tabelle stehen Fehlercodes und der Text für die Fehleranzeige im UI:

Tabelle 4: Fehleranzeige und Fehlercodes
Fehler | (Fehler-)code in TTN | Fehleranzeige UI
1. (unter 1 bar) | 102 | Pump defect
2. (über 5,5 bar) | 101 | Got stuck
Kein Fehler | 100 | None

Technische Spezifikation - Smarte Gartenbewässerung

### 5. Spezifikation der Hardware

### 5.1 Einzelteile

Nachfolgend aufgelistete Komponenten wurden von uns gezielt herausgesucht. Wir haben auf die Kompatibilität zwischen den Teilen geachtet und wenn nötig auch passende Adapter besorgt.
Ein detaillierter Schaltplan und Bauplan für die Bewässerungsanalge folgt demnächst.

Auflistung aller elektronischen Komponenten:

Tabelle 5: Elektronische Komponenten

Name | Beschreibung | Anwendungen | Schnittstellen & Spannungsbelegung | Bild
LoRa32 Mikrocontrolle r | Mikrocontroller board, wie ESP32 + LoRaWAN-Ante nne | Entwicklerboard, Steuerung, Regelung, Berechnungen, Drahtlose Verbindung mit WLAN, Bluetooth, LoRaWAN | Eingang 5V(default) Eingang 3.3V(option) Ausgang 5V, 3.3V | https://www.makershop.de/plattformen/esp8266/ttgo-esp32-paxcounter-lora/
Coolty High Pressure Diaphragm Water Pump | Pumpe | Wasser pumpen | Betriebsspannung DC 12V 100PSI 4L/min | https://amzn.to/3zsKp1O
AZDelivery 4-relay module 5 V | Relais | Steuerung der Pumpe | Eingang 5V/3V Aussgang max 250V/10A AC, 30V/10A DC | https://amzn.to/3iHNncN

Technische Spezifikation - Smarte Gartenbewässerung

EXLECO 12 V NC G1/2 Inch Electro Solenoid Valve | Magnetventil | Schließen des Wasserdurchflusses nach der Pumpe | G 1/2“ Betriebsspannung DC 12 V | https://amzn.to/3goN8BY
G1/4 inch pressure sensor | Wasserdruck-sensor | Messung des Wasserdrucks | Betriebsspannung DC 5 V G 1/4" (muss durch Spannungsteiler mit Lora32 verbinden) | https://amzn.to/3iDe3vh
ARCELI YF-S201 1-30L/min Water Flow Meter | Durchfluss-sensor | Messung des Wasserdurchflusses | The lowest rated operating voltage: DC4.5 5V-24V. Maximum working current: 15mA (DC 5V) Working Voltage Range: DC 5~18V | https://amzn.to/3xmhiM0
Aukru Ultrasonic Module HC-SR04 | Ultraschall-sensor | Messung des Wasserstandes | Static Current(Max) :2mA ; Electrical Level Eingang:5V. ranging distance: 2cm~500 cm resolution: 0.3 cm | https://amzn.to/3gmvwGU

Technische Spezifikation - Smarte Gartenbewässerung

DHT22 Digital Temperature and Humidity Sensor AM2302 | Temperatur-sensor (optional) | Messung der Temperatur und Luftfeuchtigkeit | Betriebsspannung 3.3V | https://amzn.to/3xkpc8r
AZDelivery Soil Moisture Sensor Hygrometer Module V1.2 | Bodenfeuchtig-keitssensor | Messung der Bodenfeuchte | Eingang 5V Ausgang 3.3V | https://amzn.to/3pSUmkS

Zusätzlich werden noch ein Steckbrett und Kabel zur Verbindung der Komponenten eingesetzt.

Technische Spezifikation - Smarte Gartenbewässerung

Auflistung Bewässerungskomponenten:

Tabelle 6: Bewässerungskomponenten

Name | Beschreibung | Anwendungen | Schnittstellen & Spannungsbelegung | Bild
Flexible Tube TX | Verbindung Schlauch | Verbindung der Teile für den Wasserfluss | 13 mm x 3 mm (1/2 Inch), 5 m Long PVC Hose with Fabric | https://amzn.to/3xr0hjP
Homgif Garden Irrigation System, Micro Drip Irrigation Kit | Bewässerung Schlauch (Drip System) | Beförderung des Wassers nach Magnetventil zu den Beeten, Bewässerung der Pflanzen | 30 m Schlauch bis zu 35-40 m 2 bewässern | https://amzn.to/3xlwLvH
T-piece with external/intern al/external thread | Schlauchverbing dung Schlauch Wasserdrucksse nsor | Anschluss des Wasserdrucksensors an der Wasserleitung | Size: G ½” max. Druck: 16 bar | https://amzn.to/3iElBy3
Threading Adapter | Wasserdrucksen sor Adapter | Adapter um Wasserdrucksensor mit T-Stück zu verbiWden | NPT 1/2 Male to G 1/4 Female | https://koolance.com/threading-ada pter-npt-1-2-male-to-g-1-4-female-a dt-n12m-g14f

Technische Spezifikation - Smarte Gartenbewässerung

Gardena Tap Connector | Schlauchverbing dung Schlauch Ventil-Drip System | Verbindung nach dem Magnetventil mit dem Drip-System | 21mm bzw. 1/2 Zoll zum Gartenschlauch (Gardena-Anschluss) | https://amzn.to/3gx6jIK

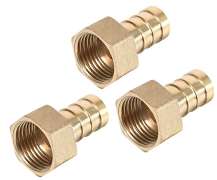
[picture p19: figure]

Sourcing Map 3 x Brass Hose Connector | Schlauchverbind ung Sensor zum Schlauch | Verbindung der Komponenten mit dem Verbindungsschlauch | Size: 14mm spike x G1/2 socket; Total length: 35mm; Hex width: 23mm; Spike length: 23mm | https://amzn.to/3wkJpuK
BGS 8095-12x20 | Hose Clamps | Befestigung der Schläuche zu den Komponenten (festziehen) | 12 x 20 mm | 10 Pieces | https://amzn.to/3gwqlmL
Hose Clamps 2 | Hose Clamps | Befestigung der Schläuche zu den Komponenten (festziehen) (andere Größe) | 8x12 mm, Stainless Steel, 10 pcs. | https://amzn.to/3gBAw9B

Technische Spezifikation - Smarte Gartenbewässerung

### 5.2 Schaltplan

Nachfolgend ist der Schaltplan für unser umgesetztes System:

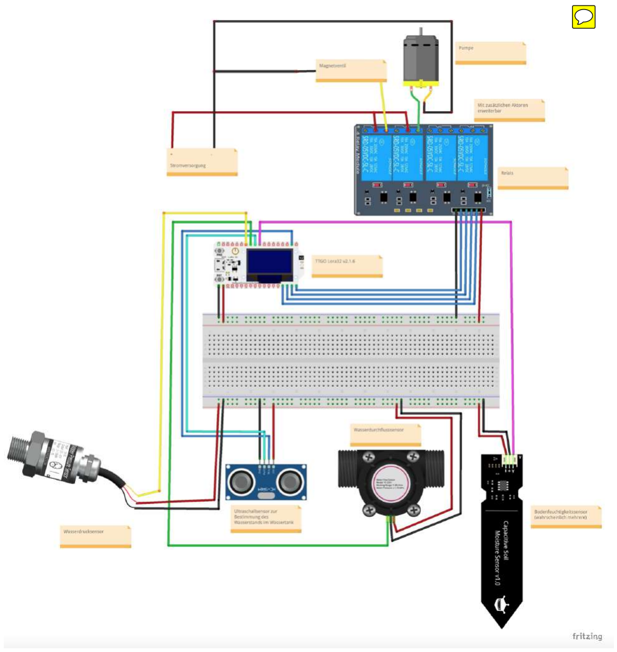
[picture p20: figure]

Abbildung 18: Schaltplan

Technische Spezifikation - Smarte Gartenbewässerung

Da das System modular erweiterbar ist, bleibt auch der Schaltplan dynamisch und veränderbar. Je nachdem welche und wie viele Aktoren und Sensoren angeschlossen sind, verändert sich der Schaltplan. Der Grundaufbau bleibt jedoch der gleich:
- Sensoren werden an die Stromversorgung und Masse angeschlossen (+ und -) und
mit | einem | (oder | in einigen Fällen auch mehreren) Pins mit dem
Lora32-Mikrocontroller verbunden. Je nachdem welches Signal die Sensoren ausgeben (digital, analog, interrupt), müssen sie an passende Pins angeschlossen werden.
- Aktoren werden über ein Relais gesteuert. D. h. der Mikrocontroller ist nicht direkt mit dem Aktor, sondern nur mit dem Relais verbunden. Das liegt daran, da die Aktoren wesentlich mehr Strom benötigen, als der Lora32 liefern kann. Weitere Aktoren würden also ebenfalls an ein Relais und eine andere externe Stromquelle
(z. B. Solaranlage im Urban Garden) verbunden werden.

Technische Spezifikation - Smarte Gartenbewässerung

### 5.3 Halterung für den Ultraschallsensor

Zur Wasserstandsmessung wird ein Ultraschallsensor verwendet, der im Deckel vom Wassertank angebracht wird. Damit er angebracht werden kann, wurde eine Halterung entwickelt und 3D-gedruckt. Somit kann der Sensor in die Halterung gesteckt werden und die Halterung an den Deckel geklebt werden und der Sensor bleibt unbeschädigt.
In nachfolgendem Bild kann der Deckel des Wassertanks und als Referenz der Ultraschallsensor gesehen werden:

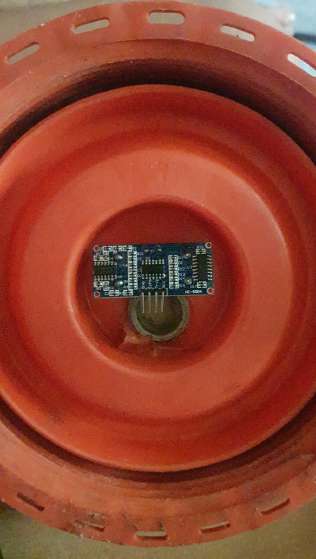
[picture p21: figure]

Abbildung 19: Wassertankdeckel
Zum Erstellen der Halterung wurde der Sensor vermessen und die Halterung in CAD konstruiert:

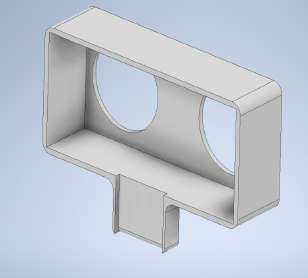
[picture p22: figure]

Abbildung 20: CAD-Konstruktion vom Halter

Technische Spezifikation - Smarte Gartenbewässerung

Anschließend wurde die Halterung an der HTW in einem 3D-Drucker gedruckt.
In folgenden Bildern kann gesehen werden, wie der Sensor in der Halterung angebracht ist:

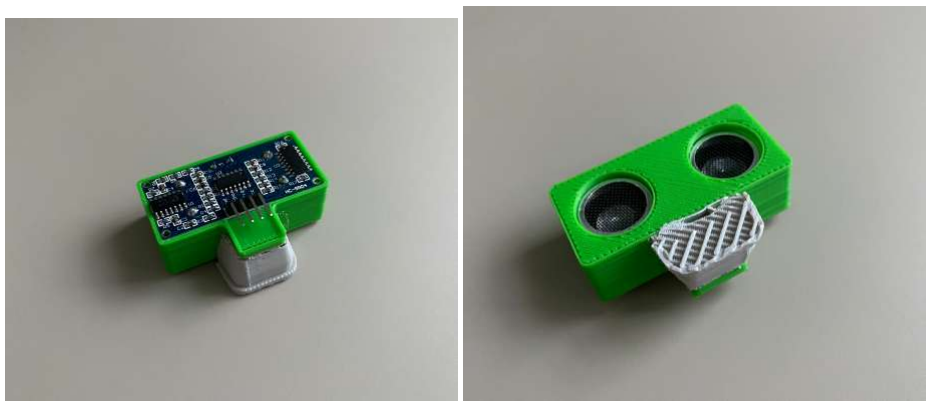
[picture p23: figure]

Abbildung 21: Ultraschallsensor in der Halterung

Technische Spezifikation - Smarte Gartenbewässerung

### 5.4 Gesamtaufbau

Anhand des Schaltplans wurde das System komplett aufgebaut.

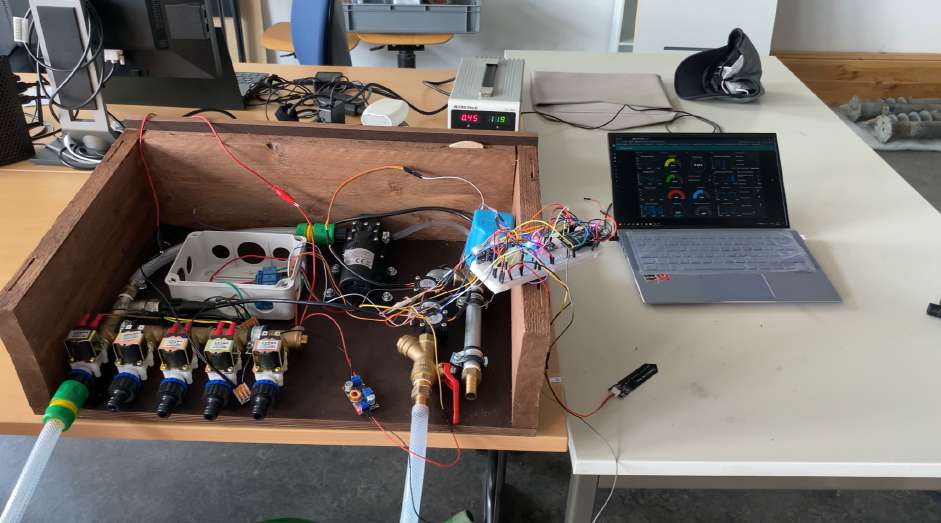
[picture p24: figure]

Abbildung 22: Bild des aufgebauten Gesamtsystems

Als externe Stromversorgung wurde hierbei ein Labornetzteil verwendet, um die Aktoren mit Strom zu versorgen. Der Mikrocontroller ist mit Hilfe eines Spannungswandler mit der Stromversorgung verbunden, da er weniger Spannung als die Aktoren benötigt.

Das komplette System und weitere Erklärungen sind in nachfolgendem YouTube-Video zu seben, das von uns erstellt wurde:
https://www.youtube.com/watch?v=hPiacfdj6qs

Hier kann gesehen werden, dass bereits fleißig an Erweiterungen und zusätzlichen Funktionen von Herr Holger Martin gearbeitet wird. An dieser Stelle auch nochmal vielen Dank an Holger, der uns beim Aufbau unterstützt hat und das Projekt noch spaßiger und spannender gemacht hat.

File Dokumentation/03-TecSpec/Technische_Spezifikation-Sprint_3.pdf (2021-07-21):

Technische Spezifikation - Smarte Gartenbewässerung

# Technische Spezifikation

# Smarte Gartenbewässerung über LoRaWAN

Mitarbeiter und Autoren:

- Rami Hammouda
- Khac Hoa Le
- Jaro Machnow

Letzte Änderung: 21.07.2021

Version: 1.5

21.07.2021 | Seite 1 von 39

Technische Spezifikation - Smarte Gartenbewässerung

Inhaltsverzeichnis

1. Einleitung | 4
1.1 Überblick | 4
1.2 Definitionen und Abkürzungen | 4
1.3 Vorhandene Dokumente | 4
2. Prozessüberblick | 4
2.1 Realisierungsprozess | 5
2.2 Fachlicher Workflow | 7
2.3 Checkliste | 8
3. Systemarchitektur und Infrastruktur | 10
3.1 Systemarchitektur | 10
3.2 Beschreibung der Komponenten | 11
4. Technische Spezifikation der Software | 12
4.1 Überblick Software-Komponenten | 12
4.2 Schnittstellen zwischen den Komponenten | 14
4.3 Technologiestack | 15
4.4 Anmeldedaten für TTN | 16
4.5 Erste Testphase - Senden und Empfangen von Daten über TTN | 17
4.6 Entwicklung der User Interface (UI) | 23
4.7 Integration von Telegram | 25
4.8 Lora32-Komponente: Klassendiagramm | 26
4.9 Autonome Steuerung | 27
4.10 Fehlererkennung und -behandlung | 29
5. Spezifikation der Hardware | 30
5.1 Einzelteile | 30
5.2 Schaltplan | 35
5.3 Halterung für den Ultraschallsensor | 37
5.4 Gesamtaufbau | 39

Technische Spezifikation - Smarte Gartenbewässerung

Versionshistorie

Version | Datum | Verantwortlich | Änderung
1.0 | 29.05.2021 | Jaro Machnow | Dokumenterstellung
1.1 | 06.06.2021 | Jaro, Hoa Le, Rami | Ergänzungen
1.2 | 15.06.2021 | Jaro, Hoa Le, Rami | Ergänzungen
1.3 | 16.06.2021 | Rami, Hoa, Jaro | Vervollständigung Sprint 1
1.4 | 15.07.2021 | Jaro, Hoa Le, Rami | Ergänzungen
1.5 | 21.07.2021 | Jaro, Hoa Le, Rami | Vervollständigungen Sprint 3

Technische Spezifikation - Smarte Gartenbewässerung

### 1. Einleitung

### 1.1 Überblick

Es wird eine smarte und möglichst preisgünstige und überwachte Bewässerung von Beeten per Netzwerksteuerung über das The-Things-Network (TTN) gebaut. Im Urban Garden kontrolliert ein Mikrocontroller entsprechend der über das Netzwerk gesendeten Nutzereingaben oder eines autonomen Workflows verschiedene Sensoren und Aktoren. Mit Hilfe einer LoRaWAN-Antenne werden die Daten der Sensoren vom Urban Garden aus in das Netzwerk gesendet und können auf einem entfernten Computer ausgelesen werden und als Visualisierung auf OpenSenseMap.org angesehen werden.

Zu den Mechanismen der autonomen Steuerung gehören vor allem das Abschalten des Wasserflusses im Falle eines Lecks und das eigenständige Starten der Bewässerung beim Erreichen einer bestimmten Bodenfeuchte.

Für alle eingebauten Komponenten und Funktionen gilt der Grundsatz, dass das System in Zukunft leicht modular erweitert werden kann.

### 1.2 Definitionen und Abkürzungen

LoRaWan -Long Range Wide Area Network TTN - The Things Network

### 1.3 Vorhandene Dokumente

Tabelle 1: Vohandene Dokumente

Dokument | Autor(en) | Datum
Lastenheft | Rami Hammouda, Khac Hoa Le, Jaro Machnow | 28.04.2021
Lastenheft + Kommentare | + Prof. Dr. Mohammad Abuosba | 30.04.2021
Anforderung-Email | Holger Martin | 10.04.2021
Pflichtenheft | Rami Hammouda, Khac Hoa Le, Jaro Machnow | 19.05.2021
Pflichtenheft + Kommentare | + Prof. Dr. Mohammad Abuosba | 25.05.2021

Technische Spezifikation - Smarte Gartenbewässerung

### 2. Prozessüberblick

### 2.1 Realisierungsprozess

Nachfolgend ist eine Darstellung aller Funktionen und deren Unterteilung im Projekt:


Abbildung 1: Übersicht über die Aufgabenstruktur

Für die Realisierung des Projektes ist es zuerst nötig, alle notwendigen Teile herauszusuchen und zu bestellen. Dann kann damit begonnen werden die Funktionsfähigkeit des Hauptziels des Projektes sicherzustellen: Das Senden und Empfangen von Daten vom Urban Garden über das LoRaWAN-Netzwerk. Danach können parallel die Nutzerschnittstellen mit TTN verbunden und programmiert werden und der Mikrocontroller mit den zugehörigen

Technische Spezifikation - Smarte Gartenbewässerung

Komponenten eingerichtet werden. Zum Schluss wird das gesamte Bewässerungssystem mit allen Komponenten zusammengebaut und im Urban Garden installiert.
Der Realisierungsprozess ist in folgendem Diagramm dargestellt:


Abbildung 2: Diagramm des Realisisierungsprozesses

Technische Spezifikation - Smarte Gartenbewässerung

### 2.2 Fachlicher Workflow

Nachfolgen ist das Diagramm des fachlichen Workflows zu sehen. Hier kann die Zusammenarbeit der Software und Hardware gesehen werden und der Ablauf bei Benutzung, Überwachung und Steuerung des Systems.


Abbildung 3: Fachlicher Workflow

Technische Spezifikation - Smarte Gartenbewässerung

### 2.3 Checkliste

Zur Strukturierung unserer Arbeit und um zu wissen, was schon gemacht wurde und was noch zu erledigen ist, haben wir folgende Checkliste erstellt. Die Checkliste beinhaltet aktuell nur Punkte, die mit der Software im Zusammenhang stehen (für den 1. Sprint).

Controlling Sensors, Actors:

Collect current ambient parameters (Temperatur sensor, Humidity sensor, Air pressure sensor.. )
Collect current water level in water tank (Ultrasound sensor)
Collect current water hose parameters (Water pressure sensor, Water flow sensor) Control Actors (Water pump, Magnetic valve)

On LoraWan Server:

Send collected sensor data to TTN Network
Operate with ABP Mode or OTAA Mode (prefer OTAA) Support float decode payload
Support int decode payload
Binding Server with opensensemap.org

Operate Actors:

Remote control actors manually
Actors operates itself automatically based on pre-configuration Auto Mode and Manual Mode should be selectable

Sensor Data Visualization:

Simple sensor data are visualizated by opensensemap
Complex sensor data will be visualizated by a self development UI

Technische Spezifikation - Smarte Gartenbewässerung

UI Development:

Create a UI to get all current information of system
Control actors through simple user-friendly UI like button, not on JSON UI (comply to requirement from Mr. Prof. Dr.-Ing. Abuosba )
Pre-configuration parameters should be changeable (e.g through input fields) (comply to suggestion from Mr. Holger Martin )

Options:

An UI on mobile for convenient monitoring Send Notification to user for alert

Technische Spezifikation - Smarte Gartenbewässerung

### 3. Systemarchitektur und Infrastruktur

### 3.1 Systemarchitektur


Abbildung 4: Komponentendiagramm

Technische Spezifikation - Smarte Gartenbewässerung

### 3.2 Beschreibung der Komponenten

Das Komponentendiagramm zeigt die verschiedenen Schichten des Bewässerungssystems:
- Ganz oben sind die Komponenten, mit denen der Nutzer interagieren kann. Dazu gehören die Anwendung und die OpenSenseMap. Bei der Anwendung sieht der Nutzer das Dashboard, in dem Sensordaten angezeigt werden können und Aktoren per Knopfdruck aktiviert oder deaktiviert werden können. Zudem kann die autonome Steuerung aktiviert werden. Die OpenSenseMap zeigt eine Karte und die Sensordaten für den Standort des Urban Gardens.
- In der Mitte befinden sich Komponenten, die die obere Anwendungsschicht mit den Sensoren und Aktoren im Urban Garden verbinden. Dazu gehören das TheThingsNetwork und der Lora32-Mikrocontroller. Über diese beiden Daten kommen die Sensordaten zur Nutzeranwendung und die Nutzereingaben zu den Aktoren. Die Kommunikation bzw. Übertragung der Daten erfolgt hier über das LoRaWan-Netzwerk und über das Internet. Nähere Informationen sind dazu in Punkt 4.2 nachzulesen.
- Unten befinden sich die Komponenten, die direkt im Urban Garden agieren, also alle Sensoren und Akoren. Dazu gehören: Wasserdrucksensor, Wasserdurchflusssensor, Wasserstandsensor, Bodenfeuchtigkeitssensor, Pumpe und Magnetventil. Diese Komponenten sind mit Lora32 verbunden und werden dadurch überwacht und gesteuert.

Technische Spezifikation - Smarte Gartenbewässerung

### 4. Technische Spezifikation der Software

### 4.1 Überblick Software-Komponenten


Abbildung 5: Komponentendiagramm Software

Technische Spezifikation - Smarte Gartenbewässerung

Beschreibung der Software-Komponenten:

Tabelle 2: Software-Komponenten

SW Komponente | Funktionen | Sprache/Typ
Anwendung (geplant) | -Daten empfangen und anzeigen - Daten auswerten - Daten senden - Alles wird in einem Dashboard angezeigt | JavaScript (Node Js)
Opensensemap (geplant) | -Anzeigen der Messdaten auf einer Karte | Website Service als Client
Telegram (geplant) | -Schnell und aktuell die Daten und den Status vom System abrufen | API Service als Client
Lora32 (Software) | -Sensorendaten abrufen - Aktoren steuern - Signal schicken/empfangen. | Programming language C++
TTN | -Zentraler Server für LoRaWAN - Schnittstelle zwischen LoRaWAN und Client. - Datenbank: Automatische Speicherung der Daten einer Woche | Website Server

Technische Spezifikation - Smarte Gartenbewässerung

### 4.2 Schnittstellen zwischen den Komponenten

Die Datenübermittlung zwischen dem LoRa32-Mikrocontroller und der Anwendung erfolgt in mehreren Schritten:
1. LoRa32 sendet die Daten an TTN-Gateways mit Hilfe der LoRaWan-Antenne.
2. Das Gateway schickt die Daten weiter ins Internet an die TTN-Cloud durch HTTP.
3. Die Anwendung ist mit der TTN-Cloud verbunden und erhält so die Daten.

Die TTN-Cloud dient dabei zugleich als Datenbank und speichert automatische die Daten einer Woche. Die Anwendung dient als grafische Benutzeroberfläche, die es dem Nutzer ermöglicht die Daten aus dem System auszulesen und das System fernzusteuern. Umgekehrt, also von der Anwendung zum LoRa32, funktioniert der Vorgang analog:
1. Der Nutzer gibt Daten in der Anwendung ein. Die Daten werden an die TTN-Cloud übermittelt.
2. Die TTN-Cloud übermittelt die Daten über HTTP an das TTN-Gateway
3. Mit Hilfe der LoRaWan-Antenne werden die Daten vom Gateway an den LoRa32-Mikrocontroller gesendet.
Die OpenSenseMap auch mit der TTN-Cloud verknüpft, um Daten anzuzeigen. Das funktioniert auf die gleiche Weise, wie bei der Anwendung. OpenSenseMap dient als weitere Benutzerschnittstelle.
Zudem wird Telegram benutzt, um eine schnelle und unkomplizierte Kommunikation des Nutzers mit dem System zu ermöglichen. Telegram ist direkt mit der Anwendung verknüpft.

Technische Spezifikation - Smarte Gartenbewässerung

### 4.3 Technologiestack

Folgender Technologiestack wird für die Erstellung der Software für die Kommunikatin über LoRaWan verwendet:

Tabelle 3: Technologiestack

Operation System: | -Windows 10/(Linux)
IDE: | -Visual Studio Code - Platform IO
Framework: | -Arduino
Abhängigkeiten: | -MCCI LoraWAN LMIC Library v3.3 - Adafruit Unified Sensor v1.1.4 - DHT sensor library v1.4.2
Protokolle: | -MQTT - HTTP
Drahtlose Verbindung/ Kommunikation: | - LoRaWAN (Long Range Wide Area Network)
Tools: | -MQTT Mosquito - MQTT Explorer
Server: | -TTN (thethingsnetwork)
UI Programmierung: | -JavaScript - NodeJS
Hardware Programmierung: | -C++
Hardware: | -Lora32 (TTGO)

Technische Spezifikation - Smarte Gartenbewässerung

### 4.4 Anmeldedaten für TTN

Mit folgenden Daten kann man sich beim TTN-Account unseres Teams anmelden, Einstellungen vornehmen und empfangene Sensordaten einsehen und Aktoren steuern:

THETHINGSNETWORK.ORG (Legacy V2 Console)
User name: htwgardenproject
Email address: htwgardenss21@gmail.com Password: htwgarden2021

Technische Spezifikation - Smarte Gartenbewässerung

### 4.5 Erste Testphase - Senden und Empfangen von Daten über TTN

Bevor die Verbindung der TTN-Server mit der Anwendung, OpenSenseMap und Telegram erstellt wird, wird zunächst die Kommunikation über LoRaWan mit MQTT-Mosquito, MQTT.Fx und MQTT-Explorer getestet.
Wenn die Daten von LoRa32 sicher erzeugt werden, wird LoRa32 mit dem TTN-Server verbunden. Bei der TTN-Cloud können Uplinks (Signal von Sensoren) gelesen werden und die Downlinks (Signal zur Sensoren) geschickt werden. Das Emfpangen von Sensordaten und das Schicken von Daten zur Steuerung von Aktoren werden getestet.
In der Testschaltung werden die Daten des DHT22 Temperatur- und Luftfeuchtigkeitssensors vom Lora32 erfasst. Dann werden die Daten weiter an TNN gesendet. Bei jedem Senden leuchtet die grüne LED. Zusätzlich kann ein Signal von TTN aus gesendet werden um die rote LED an- bzw. auszuschalten.
Bei dem ersten Test stand uns ein Lora32 v1 zur Verfügung. Ein Bild dieser Schaltung ist in nachfolgender Abbildung zu sehen:


Abbildung 6: Aufbau der Schaltung für den Test der LoRaWan-Verbindung (Lora32 V1 ohn Oled)

Technische Spezifikation - Smarte Gartenbewässerung

Wenig später stand die neuere Version des TTGO Lora32 zur Verfügung: Lora32 OLED V2.1.6. Auf dem Display werden direkt die gemessenen Sensordaten angezeigt. So kann geprüft werden, ob die Daten korrekt an TTN übertragen werden und gleiche Werte angezeigt werden.


Abbildung7: Aufbau der Schaltung für den Test der LoRaWan-Verbindung (Lora32 OLED V2.1.6)

In Gitlab → Software → Node-Lora32 → src → main.cpp ist der C++ Code zu finden, der auf

dem Lora32 installiert ist. Grundlegend gibt es eine Funktion zum Auslesen der Sensordaten des DHT22, zum Steuern von einer grünen und einer roten LED, zur Umwandlung der Daten in Byte mit dem Encoder, um sie versenden zu können und zum Senden der Daten über die Lora-Antenne.
Die Daten werden von einem TTN-Gateway empfangen und ins TTN-Netzwerk zu einem TTN-Server weitergeleitet. Mit dem Tool MQTT-Mosquitto oder MQTT-Explorer oder mit der Website von von TTN können wir auf die Daten in TNN zugreifen und die Sensordaten auslesen.

Technische Spezifikation - Smarte Gartenbewässerung

1. MQTT-Mosquito (als Client betrachtet)
Folgende Daten werden zur Verbindung über MQTT benötigt (um auf die Daten auf dem Daten TTN-Server zuzugreifen):
App ID on TTN: mygardenproject
Access key on TTN: ttn-account-v2.60jnFj-pF6rapK8BtiWsr2CQXM8TufQspWzjreeI2Zc

Folgende Befehle müssen in die Konsole eingegeben werden :
Active Mosquito service:
net start mosquitto
Subscribe our topic:
mosquitto_sub -h eu.thethings.network -p 1883 -d -u mygardenproject -P ttn-account-v2.60jnFj-pF6rapK8BtiWsr2CQXM8TufQspWzjreeI2Zc -t #

In nachfolgendem Bild sieht man die Ausgabe in der CMD ür MQTT-Mosquitto.


Abbildung 8: MQTT Mosquito


Technische Spezifikation - Smarte Gartenbewässerung

2. MQTT-Explorer (Client)
Alternativ können die Daten auch mit Hilfe von MQTT-Explorer ausgelesen werden. Hier kann sich der User mit den selben Anmeldedaten ins System einloggen.

Abbildung 9: Einloggen bei MQTT-Explorer

Hier kann die Ausgabe im MQTT-Explorer gesehen werden:

Abbildung 10: Ausgabe der Sensordaten MQTT-Explorer

Technische Spezifikation - Smarte Gartenbewässerung

3. TTN-Website (Server + Client)
Die schönste und einfachste Möglichkeit, um die Daten auszulesen, ist das direkte Nutzen der Website von TTN.
Um die Daten dekodieren zu können, muss zuerst das Payload-Format auf der Website von TTN geschrieben werden, um die empfangenen Daten von Byte zurück in ein lesbares Format umzuwandeln.
In folgendem Bild ist die Funktion zum Dekodieren zu sehen:


Abbildung 11: Payload-Dekodier-Code

Technische Spezifikation - Smarte Gartenbewässerung

Dann können die Daten bei TTN gelesen werden:


Abbildung 12: Datenausgabe TNN

Technische Spezifikation - Smarte Gartenbewässerung

### 4.6 Entwicklung der User Interface (UI)

Entsprechend der ersten Testphase, in der in der Testschaltung ein DHT22 Temperatur- und Luftfeuchtigkeitssensor und zwei LEDs verbaut waren, wurde ein User Interface erstellt, das folgende Funktionen hat:
- Zahlenwerte der aktuellen Sensordaten (Temperatur, Luftfeuchtigkeit, Feel-Like-Temperatur)
- Verlaufsdiagramme für diese Sensorwerte
- Schalter für den Wechsel zwischen Auto und Manual Mode
- Schalter für das Aktivieren/Deaktivieren des Aktors (LED) im Manual Mode
- Hinweis-Leuchte, die grün leuchtet, sobald ein Signal über TTN empfangen wird
- Diagramme für Signal Noise und Signal Strength (Werte sind gut, wenn: Signal Noise zwischen -20 dB bis 10 dB und Signal Strength zwischen -120 dBm bis -30 dBm) Das User-Interface wurde mit Node-Red entwickelt und mit TTN über eine Schnittstelle verbunden.
Nachfolgend ist das User Interface zu sehen:


Abbildung 13: Erstes Test-UI

Technische Spezifikation - Smarte Gartenbewässerung

Nachdem das System mit den richtigen Sensoren und Aktoren erweitert wurde, musste auch das User Interface erweitert werden.
Nachfolgende Informationen bzw. Aktionen können im finalen User Interface gesehen und benutzt werden:
- Gauge: Aktuelle Werte der Sensoren, die einen Minimal- und Maximalwert haben. (Temperatur, LuftFeuchtigkeit, Bodentrockenheit, Luftdruck, Wasserdruck, Druck in Leitung und Wasserstand)
- Histogram: Verlauf der Sensordaten, um einen zeitlichen Überblick zu erhalten. (Temperatur, Luftfeuchtigkeit, Bodentrockenheit, Wasserdruck, Wasserstand, Wasserdurchfluss-Geschwindigkeit, Strength of Signal und Signal Noise)
- Text: Aktuelle Werte von Sensoren, deren Werte kein Maximum haben (Wasserdurchfluss Geschwindigkeit, Wasserdurchfluss Volumen)
- LED: visualisiert den aktuellen Status von Aktor und den Update-Status: (Update-Signal, Ventil und Pumpe Status)
- Switch/Schalter: Wechsel zwischen verschiedenen Modi /Zuständen
(Manuell oder Auto Modus, Turn On/Off Watering System in Manual Mode und Debug Mode)
- Slider: Steuerungswerte, die zum autonomen Betrieb vom System gehören. (Bodenfeuchtigkeit zu an/aus, Wasserstand zu aus, Wasservolumen zu aus)


Abbildung 14: Finales UI

Technische Spezifikation - Smarte Gartenbewässerung

### 4.7 Integration von Telegram

Um eine weitere und sehr einfache Möglichkeit für den Nutzer bereitzustellen, um die Sensorwerte auszulesen. Deswegen wurde unser System mit Hilfe der Telegram Bot API mit dem Telegram-Messenger verbunden.
Der Nutzer kann somit schnell wichtige Informationen über aktuell Stand von Garten abfragen. Der Admin bekommt zudem jedes mal eine Nachricht, wenn die Bewässerung aktiviert oder deaktiviert wurde.
Nachfolgend sind Screenshots aus der Telegram-App auf einem Android-Smartphone.


Abbildung 15: Screenshots von Telegram

Daten:
Telegram bot: HTWGarden (nicht HTW GardenSS21, da ist die alte Version)

Befehle:
- /help: allgemeine Informationen und Hinweise
- /status: aktuellen Stand vom Garten abfragen

Technische Spezifikation - Smarte Gartenbewässerung

### 4.8 Lora32-Komponente: Klassendiagramm

Um das System Modular zu gestalten und es einfach zu machen später neue Sensoren und Aktoren hinzuzufügen, wurde folgende Klassenhierachie für die Komponenten, die an den Lora32 angeschlossen werden, definiert:


Abbildung 16: Klassendiagramm

Die Klassen Actor und Sensor erben von der Klasse Component. In der Klasse Component werden die Pins am Lora32 verwaltet:
- wird ein Sensor oder Aktor mit einem Pin registriert, kann dieser nicht nochmal verwendet werden
- es können nur Pins verwendet werden, die der Lora32 überhaupt hat

Technische Spezifikation - Smarte Gartenbewässerung

Von der Klasse Sensor erben die verwendeten Sensoren. Diese sind in einzelnen Klassen, da die Werte von jedem Sensor auf unterschiedliche Art und Weise ausgelesen werden müssen (analog, digital, interrupt).
Die Aktoren agieren alle gleich: man kann sie ein- oder ausschalten. Allerdings gibt es unterschiedliche Relais-Arten. Deswegen muss noch der bool-Wert “invert” hinzugefügt werden. Unser Relais schaltet in den Zustand “ein”, wenn kein Signal anliegt. Das Signal muss also dementsprechend invertiert werden.
Zusätzlich gibt es noch eine Klasse Automation, die in der Set-Funktion einen Ist-Sensor-Wert, einen Operator als string, einen Soll-Sensor-Wert, den Actor und einen bool, ob der Aktor aktiviert oder deaktiviert werden soll, entgegen nimmt. Wird die Funktion aufgerufen, werden die Werte entsprechend dem Operator verglichen und der Aktor aktiviert oder deaktiviert.

### 4.9 Autonome Steuerung

Unser System kann autonom und ganz unabhängig von der Verbindung mit TTN und damit auch von Eingaben des Nutzers betrieben werden.
Dazu muss der Nutzer einen Schalter (Master-Switch) umlegen, um die autonome Steuerung zu aktivieren. Diese Information wird dann an den Mikrocontroller gesendet, woraufhin dieser unabhängig von LoraWan die Bewässerung steuern kann.
Ist der autonome Modus aktiviert, können Parameter für die autonome Steuerung mit vier Slidern eingestellt werden:
- Moisture-On: ab welchem Trockenheitswert soll die Bewässerung aktiviert werden
- Moisture-Off: unter welchem Trockenheitswert soll die Bewässerung deaktiviert werden
- Water Lvl-Off: unter welchem Wasserstandswert soll die Bewässerung deaktivert werden
- Water Vol-Off: ab welchem Wert für das durchgeflossene Wasser soll die Bewässerung deaktiviert werden

Hinweis: Water Vol-Off funktioniert mit Hilfe von FreeRTOS (Free Real Time Operating System) möglich und bis jetzt nur ein experimentelles Feature. Nachdem der eingestellte


Technische Spezifikation - Smarte Gartenbewässerung

Water Vol-Off Wert erreicht wird, wird das System automatisch einen Neustart machen, um den Water-Volume-Wert wieder auf 0 zurückzusetzen

Nachfolgend können der Master-Switch und die Slider für die Parameter gesehen werden (links ist noch der Manual Mode aktiviert, rechts der Auto Mode) :

Abbildung 17: Einstellungen für die Autonome Steuerung

Technische Spezifikation - Smarte Gartenbewässerung

### 4.10 Fehlererkennung und -behandlung

Das System hat die Fähigkeit, selbst Fehler zu erkennen und die Bewässerung dann automatisch zu deaktivieren, um kein Wasser zu verschwenden und Schäden zu vermeiden. Es sind zwei Fehlerszenarien definiert:
1. Druck in der Leitung sinkt unter 1 bar (wahrscheinlich Leck oder defekte Pumpe)
2. Druck in der Leitung steigt über 5,5 bar (wahrscheinlich Verstopfung)

Die voreingestellten Werte von 1 bar und 5,5 bar sind nur zur Simulation und müssen nach dem kompletten Aufbau (mit allen Schläuchen, Verbindungsstücken und Tropfern bzw. Regnern und weiteren Teilen) neu ermittelt werden, da sich dadurch die Vorbedingungen für die Standard-Werte im System ändern.
In nachfolgender Tabelle stehen Fehlercodes und der Text für die Fehleranzeige im UI:

Tabelle 4: Fehleranzeige und Fehlercodes
Fehler | (Fehler-)code in TTN | Fehleranzeige UI
1. (unter 1 bar) | 102 | Pump defect
2. (über 5,5 bar) | 101 | Got stuck
Kein Fehler | 100 | None

Technische Spezifikation - Smarte Gartenbewässerung

### 5. Spezifikation der Hardware

### 5.1 Einzelteile

Nachfolgend aufgelistete Komponenten wurden von uns gezielt herausgesucht. Wir haben auf die Kompatibilität zwischen den Teilen geachtet und wenn nötig auch passende Adapter besorgt.
Ein detaillierter Schaltplan und Bauplan für die Bewässerungsanalge folgt demnächst.

Auflistung aller elektronischen Komponenten:

Tabelle 5: Elektronische Komponenten

Name | Beschreibung | Anwendungen | Schnittstellen & Spannungsbelegung | Bild
LoRa32 Mikrocontrolle r | Mikrocontroller board, wie ESP32 + LoRaWAN-Ante nne | Entwicklerboard, Steuerung, Regelung, Berechnungen, Drahtlose Verbindung mit WLAN, Bluetooth, LoRaWAN | Eingang 5V(default) Eingang 3.3V(option) Ausgang 5V, 3.3V | https://www.makershop.de/plattformen/esp8266/ttgo-esp32-paxcounter-lora/
Coolty High Pressure Diaphragm Water Pump | Pumpe | Wasser pumpen | Betriebsspannung DC 12V 100PSI 4L/min | https://amzn.to/3zsKp1O
AZDelivery 4-relay module 5 V | Relais | Steuerung der Pumpe | Eingang 5V/3V Aussgang max 250V/10A AC, 30V/10A DC | https://amzn.to/3iHNncN

Technische Spezifikation - Smarte Gartenbewässerung

EXLECO 12 V NC G1/2 Inch Electro Solenoid Valve | Magnetventil | Schließen des Wasserdurchflusses nach der Pumpe | G 1/2“ Betriebsspannung DC 12 V | https://amzn.to/3goN8BY
G1/4 inch pressure sensor | Wasserdruck-sensor | Messung des Wasserdrucks | Betriebsspannung DC 5 V G 1/4" (muss durch Spannungsteiler mit Lora32 verbinden) | https://amzn.to/3iDe3vh
ARCELI YF-S201 1-30L/min Water Flow Meter | Durchfluss-sensor | Messung des Wasserdurchflusses | The lowest rated operating voltage: DC4.5 5V-24V. Maximum working current: 15mA (DC 5V) Working Voltage Range: DC 5~18V | https://amzn.to/3xmhiM0
Aukru Ultrasonic Module HC-SR04 | Ultraschall-sensor | Messung des Wasserstandes | Static Current(Max) :2mA ; Electrical Level Eingang:5V. ranging distance: 2cm~500 cm resolution: 0.3 cm | https://amzn.to/3gmvwGU

Technische Spezifikation - Smarte Gartenbewässerung

DHT22 Digital Temperature and Humidity Sensor AM2302 | Temperatur-sensor (optional) | Messung der Temperatur und Luftfeuchtigkeit | Betriebsspannung 3.3V | https://amzn.to/3xkpc8r
AZDelivery Soil Moisture Sensor Hygrometer Module V1.2 | Bodenfeuchtig-keitssensor | Messung der Bodenfeuchte | Eingang 5V Ausgang 3.3V | https://amzn.to/3pSUmkS

Zusätzlich werden noch ein Steckbrett und Kabel zur Verbindung der Komponenten eingesetzt.

Technische Spezifikation - Smarte Gartenbewässerung

Auflistung Bewässerungskomponenten:

Tabelle 6: Bewässerungskomponenten

Name | Beschreibung | Anwendungen | Schnittstellen & Spannungsbelegung | Bild
Flexible Tube TX | Verbindung Schlauch | Verbindung der Teile für den Wasserfluss | 13 mm x 3 mm (1/2 Inch), 5 m Long PVC Hose with Fabric | https://amzn.to/3xr0hjP
Homgif Garden Irrigation System, Micro Drip Irrigation Kit | Bewässerung Schlauch (Drip System) | Beförderung des Wassers nach Magnetventil zu den Beeten, Bewässerung der Pflanzen | 30 m Schlauch bis zu 35-40 m 2 bewässern | https://amzn.to/3xlwLvH
T-piece with external/intern al/external thread | Schlauchverbing dung Schlauch Wasserdrucksse nsor | Anschluss des Wasserdrucksensors an der Wasserleitung | Size: G ½” max. Druck: 16 bar | https://amzn.to/3iElBy3
Threading Adapter | Wasserdrucksen sor Adapter | Adapter um Wasserdrucksensor mit T-Stück zu verbiWden | NPT 1/2 Male to G 1/4 Female | https://koolance.com/threading-ada pter-npt-1-2-male-to-g-1-4-female-a dt-n12m-g14f

Technische Spezifikation - Smarte Gartenbewässerung

Gardena Tap Connector | Schlauchverbing dung Schlauch Ventil-Drip System | Verbindung nach dem Magnetventil mit dem Drip-System | 21mm bzw. 1/2 Zoll zum Gartenschlauch (Gardena-Anschluss) | https://amzn.to/3gx6jIK


Sourcing Map 3 x Brass Hose Connector | Schlauchverbind ung Sensor zum Schlauch | Verbindung der Komponenten mit dem Verbindungsschlauch | Size: 14mm spike x G1/2 socket; Total length: 35mm; Hex width: 23mm; Spike length: 23mm | https://amzn.to/3wkJpuK
BGS 8095-12x20 | Hose Clamps | Befestigung der Schläuche zu den Komponenten (festziehen) | 12 x 20 mm | 10 Pieces | https://amzn.to/3gwqlmL
Hose Clamps 2 | Hose Clamps | Befestigung der Schläuche zu den Komponenten (festziehen) (andere Größe) | 8x12 mm, Stainless Steel, 10 pcs. | https://amzn.to/3gBAw9B

Technische Spezifikation - Smarte Gartenbewässerung

### 5.2 Schaltplan

Nachfolgend ist der Schaltplan für unser umgesetztes System:


Abbildung 18: Schaltplan

Technische Spezifikation - Smarte Gartenbewässerung

Da das System modular erweiterbar ist, bleibt auch der Schaltplan dynamisch und veränderbar. Je nachdem welche und wie viele Aktoren und Sensoren angeschlossen sind, verändert sich der Schaltplan. Der Grundaufbau bleibt jedoch der gleich:
- Sensoren werden an die Stromversorgung und Masse angeschlossen (+ und -) und
mit | einem | (oder | in einigen Fällen auch mehreren) Pins mit dem
Lora32-Mikrocontroller verbunden. Je nachdem welches Signal die Sensoren ausgeben (digital, analog, interrupt), müssen sie an passende Pins angeschlossen werden.
- Aktoren werden über ein Relais gesteuert. D. h. der Mikrocontroller ist nicht direkt mit dem Aktor, sondern nur mit dem Relais verbunden. Das liegt daran, da die Aktoren wesentlich mehr Strom benötigen, als der Lora32 liefern kann. Weitere Aktoren würden also ebenfalls an ein Relais und eine andere externe Stromquelle
(z. B. Solaranlage im Urban Garden) verbunden werden.

Technische Spezifikation - Smarte Gartenbewässerung

### 5.3 Halterung für den Ultraschallsensor

Zur Wasserstandsmessung wird ein Ultraschallsensor verwendet, der im Deckel vom Wassertank angebracht wird. Damit er angebracht werden kann, wurde eine Halterung entwickelt und 3D-gedruckt. Somit kann der Sensor in die Halterung gesteckt werden und die Halterung an den Deckel geklebt werden und der Sensor bleibt unbeschädigt.
In nachfolgendem Bild kann der Deckel des Wassertanks und als Referenz der Ultraschallsensor gesehen werden:


Abbildung 19: Wassertankdeckel
Zum Erstellen der Halterung wurde der Sensor vermessen und die Halterung in CAD konstruiert:


Abbildung 20: CAD-Konstruktion vom Halter

Technische Spezifikation - Smarte Gartenbewässerung

Anschließend wurde die Halterung an der HTW in einem 3D-Drucker gedruckt.
In folgenden Bildern kann gesehen werden, wie der Sensor in der Halterung angebracht ist:


Abbildung 21: Ultraschallsensor in der Halterung

Technische Spezifikation - Smarte Gartenbewässerung

### 5.4 Gesamtaufbau

Anhand des Schaltplans wurde das System komplett aufgebaut.


Abbildung 22: Bild des aufgebauten Gesamtsystems

Als externe Stromversorgung wurde hierbei ein Labornetzteil verwendet, um die Aktoren mit Strom zu versorgen. Der Mikrocontroller ist mit Hilfe eines Spannungswandler mit der Stromversorgung verbunden, da er weniger Spannung als die Aktoren benötigt.

Das komplette System und weitere Erklärungen sind in nachfolgendem YouTube-Video zu seben, das von uns erstellt wurde:
https://www.youtube.com/watch?v=hPiacfdj6qs

Hier kann gesehen werden, dass bereits fleißig an Erweiterungen und zusätzlichen Funktionen von Herr Holger Martin gearbeitet wird. An dieser Stelle auch nochmal vielen Dank an Holger, der uns beim Aufbau unterstützt hat und das Projekt noch spaßiger und spannender gemacht hat.

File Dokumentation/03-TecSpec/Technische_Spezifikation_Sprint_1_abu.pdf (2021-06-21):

Technische Spezifikation - Smarte Gartenbewässerung

# Technische Spezifikation

# Smarte Gartenbewässerung über LoRaWAN

Mitarbeiter und Autoren:

- Rami Hammouda
- Khac Hoa Le
- Jaro Machnow

Letzte Änderung: 16.06.2021

Version: 1.3

16.06.2021 | Seite 1 von 27

## Sehr gute tech. Spezifikation, obwohl die Komponentenbeschreibung nicht ganz vollständig ist (für dieses Sprint). Weitere Anmerkungen siehe unten!

## Wertung: TechSpec : 4,5 Punkte Anwendung : 10 Punkte

Technische Spezifikation - Smarte Gartenbewässerung

Inhaltsverzeichnis

1. Einleitung | 4
1.1 Überblick | 4
1.2 Definitionen und Abkürzungen | 4
1.3 Vorhandene Dokumente | 4
2. Prozessüberblick | 4
2.1 Realisierungsprozess | 5
2.2 Fachlicher Workflow | 7
2.3 Checkliste | 8
3. Systemarchitektur und Infrastruktur | 10
3.1 Systemarchitektur | 10
3.2 Beschreibung der Komponenten | 11
4. Technische Spezifikation der Software | 12
4.1 Überblick Komponenten | 12
4.2 Schnittstellen zwischen den Komponenten | 14
4.3 Technologiestack | 15
4.4 Anmeldedaten für TTN | 16
4.5 Testphase 1 - Senden und Empfangen von Daten über TTN | 17
5. Spezifikation der Hardware | 23
5.1 Einzelteile | 23

Technische Spezifikation - Smarte Gartenbewässerung

Versionshistorie

Version | Datum | Verantwortlich | Änderung
1.0 | 29.05.2021 | Jaro Machnow | Dokumenterstellung
1.1 | 06.06.2021 | Jaro, Hoa Le, Rami | Ergänzungen
1.2 | 15.06.2021 | Jaro, Hoa Le, Rami | Ergänzungen
1.3 | 16.06.2021 | Rami, Hoa, Jaro | Vervollständigung der Dokument

Technische Spezifikation - Smarte Gartenbewässerung

1. Einleitung
1.1 Überblick

Es wird eine smarte und möglichst preisgünstige und überwachte Bewässerung von Beeten per Netzwerksteuerung über das The-Things-Network (TTN) gebaut. Im Urban Garden kontrolliert ein Mikrocontroller entsprechend der über das Netzwerk gesendeten Nutzereingaben oder eines autonomen Workflows verschiedene Sensoren und Aktoren. Mit Hilfe einer LoRaWAN-Antenne werden die Daten der Sensoren vom Urban Garden aus in das Netzwerk gesendet und können auf einem entfernten Computer ausgelesen werden und als Visualisierung auf OpenSenseMap.org angesehen werden.

Zu den Mechanismen der autonomen Steuerung gehören vor allem das Abschalten des Wasserflusses im Falle eines Lecks und das eigenständige Starten der Bewässerung beim Erreichen einer bestimmten Bodenfeuchte.

Für alle eingebauten Komponenten und Funktionen gilt der Grundsatz, dass das System in Zukunft leicht modular erweitert werden kann.

1.2 Definitionen und Abkürzungen

LoRaWan -Long Range Wide Area Network TTN - The Things Network

1.3 Vorhandene Dokumente

Tabelle 1: Vohandene Dokumente

Dokument | Autor(en) | Datum
Lastenheft | Rami Hammouda, Khac Hoa Le, Jaro Machnow | 28.04.2021
Lastenheft + Kommentare | + Prof. Dr. Mohammad Abuosba | 30.04.2021
Anforderung-Email | Holger Martin | 10.04.2021
Pflichtenheft | Rami Hammouda, Khac Hoa Le, Jaro Machnow | 19.05.2021
Pflichtenheft + Kommentare | + Prof. Dr. Mohammad Abuosba | 25.05.2021

Technische Spezifikation - Smarte Gartenbewässerung

2. Prozessüberblick

2.1 Realisierungsprozess

Nachfolgend ist eine Darstellung aller Funktionen und deren Unterteilung im Projekt:


Abbildung 1: Übersicht über die Aufgabenstruktur

Für die Realisierung des Projektes ist es zuerst nötig, alle notwendigen Teile herauszusuchen und zu bestellen. Dann kann damit begonnen werden die Funktionsfähigkeit des Hauptziels des Projektes sicherzustellen: Das Senden und Empfangen von Daten vom Urban Garden über das LoRaWAN-Netzwerk. Danach können parallel die Nutzerschnittstellen mit TTN verbunden und programmiert werden und der Mikrocontroller mit den zugehörigen

Technische Spezifikation - Smarte Gartenbewässerung

Komponenten eingerichtet werden. Zum Schluss wird das gesamte Bewässerungssystem mit allen Komponenten zusammengebaut und im Urban Garden installiert.
Der Realisierungsprozess ist in folgendem Diagramm dargestellt:


Abbildung 2: Diagramm des Realisisierungsprozesses

Technische Spezifikation - Smarte Gartenbewässerung

2.2 Fachlicher Workflow

Nachfolgen ist das Diagramm des fachlichen Workflows zu sehen. Hier kann die Zusammenarbeit der Software und Hardware gesehen werden und der Ablauf bei Benutzung, Überwachung und Steuerung des Systems.


Abbildung 3: Fachlicher Workflow

Technische Spezifikation - Smarte Gartenbewässerung

2.3 Checkliste

Zur Strukturierung unserer Arbeit und um zu wissen, was schon gemacht wurde und was noch zu erledigen ist, haben wir folgende Checkliste erstellt. Die Checkliste beinhaltet aktuell nur Punkte, die mit der Software im Zusammenhang stehen (für den 1. Sprint).

Controlling Sensors, Actors:

Collect current ambient parameters (Temperatur sensor, Humidity sensor, Air pressure sensor.. )
Collect current water level in water tank (Ultrasound sensor)
Collect current water hose parameters (Water pressure sensor, Water flow sensor) Control Actors (Water pump, Magnetic valve)

On LoraWan Server:

Send collected sensor data to TTN Network
Operate with ABP Mode or OTAA Mode (prefer OTAA) Support float decode payload
Support int decode payload
Binding Server with opensensemap.org

Operate Actors:

Remote control actors manually
Actors operates itself automatically based on pre-configuration Auto Mode and Manual Mode should be selectable

Sensor Data Visualization:

Simple sensor data are visualizated by opensensemap
Complex sensor data will be visualizated by a self development UI

Technische Spezifikation - Smarte Gartenbewässerung

UI Development:

Create a UI to get all current information of system
Control actors through simple user-friendly UI like button, not on JSON UI (comply to requirement from Mr. Prof. Dr.-Ing. Abuosba )
Pre-configuration parameters should be changeable (e.g through input fields) (comply to suggestion from Mr. Holger Martin )

Options:

An UI on mobile for convenient monitoring Send Notification to user for alert

Technische Spezifikation - Smarte Gartenbewässerung

3. Systemarchitektur und Infrastruktur

3.1 Systemarchitektur


Abbildung 4: Komponentendiagramm

Technische Spezifikation - Smarte Gartenbewässerung

3.2 Beschreibung der Komponenten

Das | Komponentendiagramm | zeigt | die | verschiedenen | Schichten | unseres
Bewässerungssystems:
- Ganz oben sind die Komponenten, mit denen der Nutzer interagieren kann. Dazu gehören die Anwendung und die OpenSenseMap. Bei der Anwendung sieht der Nutzer das Dashboard, in dem Sensordaten angezeigt werden können und Aktoren per Knopfdruck aktiviert oder deaktiviert werden können. Zudem kann die autonome Steuerung aktiviert werden. Die OpenSenseMap zeigt eine Karte und die Sensordaten für den Standort des Urban Gardens.
- In der Mitte befinden sich Komponenten, die die obere Anwendungsschicht mit den Sensoren und Aktoren im Urban Garden verbinden. Dazu gehören das TheThingsNetwork und der Lora32-Mikrocontroller. Über diese beiden Daten kommen die Sensordaten zur Nutzeranwendung und die Nutzereingaben zu den Aktoren. Die Kommunikation bzw. Übertragung der Daten erfolgt hier über das LoRaWan-Netzwerk und über das Internet. Nähere Informationen sind dazu in Punkt
| 4.2 nachzulesen.
- Unten befinden sich die Komponenten, die direkt im Urban Garden agieren, also alle Sensoren und Akoren. Dazu gehören: Wasserdrucksensor, Wasserdurchflusssensor, Wasserstandsensor, Bodenfeuchtigkeitssensor, Pumpe und Magnetventil. Diese Komponenten sind mit Lora32 verbunden und werden dadurch überwacht und
| gesteuert.

Technische Spezifikation - Smarte Gartenbewässerung

4. Technische Spezifikation der Software

4.1 Überblick Komponenten


Abbildung 5: Komponentendiagramm Software

Technische Spezifikation - Smarte Gartenbewässerung

Beschreibung der Software-Komponenten:

Tabelle 2: Software-Komponenten

SW Komponente | Funktionen | Sprache/Typ
Anwendung (geplant) | -Daten empfangen und anzeigen - Daten auswerten - Daten senden - Alles wird in einem Dashboard angezeigt | JavaScript (Node Js)
Opensensemap (geplant) | -Anzeigen der Messdaten auf einer Karte | Website Service als Client
Telegram (geplant) | -Schnell und aktuell die Daten und den Status vom System abrufen | API Service als Client
Lora32 (Software) | -Sensorendaten abrufen - Aktoren steuern - Signal schicken/empfangen. | Programming language C++
TTN | -Zentraler Server für LoRaWAN - Schnittstelle zwischen LoRaWAN und Client. - Datenbank: Automatische Speicherung der Daten einer Woche | Website Server

Technische Spezifikation - Smarte Gartenbewässerung

4.2 Schnittstellen zwischen den Komponenten

Die Datenübermittlung zwischen dem LoRa32-Mikrocontroller und der Anwendung erfolgt in mehreren Schritten:
1. LoRa32 sendet die Daten an TTN-Gateways mit Hilfe der LoRaWan-Antenne.
2. Das Gateway schickt die Daten weiter ins Internet an die TTN-Cloud durch HTTP.
3. Die Anwendung ist mit der TTN-Cloud verbunden und erhält so die Daten.

Die TTN-Cloud dient dabei zugleich als Datenbank und speichert automatische die Daten einer Woche. Die Anwendung dient als grafische Benutzeroberfläche, die es dem Nutzer ermöglicht die Daten aus dem System auszulesen und das System fernzusteuern. Umgekehrt, also von der Anwendung zum LoRa32, funktioniert der Vorgang analog:
1. Der Nutzer gibt Daten in der Anwendung ein. Die Daten werden an die TTN-Cloud übermittelt.
2. Die TTN-Cloud übermittelt die Daten über HTTP an das TTN-Gateway
3. Mit Hilfe der LoRaWan-Antenne werden die Daten vom Gateway an den LoRa32-Mikrocontroller gesendet.
Die OpenSenseMap auch mit der TTN-Cloud verknüpft, um Daten anzuzeigen. Das funktioniert auf die gleiche Weise, wie bei der Anwendung. OpenSenseMap dient als weitere Benutzerschnittstelle.
Zudem wird Telegram benutzt, um eine schnelle und unkomplizierte Kommunikation des Nutzers mit dem System zu ermöglichen. Telegram ist direkt mit der Anwendung verknüpft.

Technische Spezifikation - Smarte Gartenbewässerung

4.3 Technologiestack

Folgender Technologiestack wird für die Erstellung der Software für die Kommunikatin über LoRaWan verwendet:

Tabelle 3: Technologiestack

Operation System: | -Windows 10/(Linux)
IDE: | -Visual Studio Code - Platform IO
Framework: | -Arduino
Abhängigkeiten: | -MCCI LoraWAN LMIC Library v3.3 - Adafruit Unified Sensor v1.1.4 - DHT sensor library v1.4.2
Protokolle: | -MQTT - HTTP
Drahtlose Verbindung/ Kommunikation: | - LoRaWAN (Long Range Wide Area Network)
Tools: | -MQTT Mosquito - MQTT Explorer
Server: | -TTN (thethingsnetwork)
UI Programmierung: | -JavaScript - NodeJS
Hardware Programmierung: | -C++
Hardware: | -Lora32 (TTGO)

Technische Spezifikation - Smarte Gartenbewässerung

4.4 Anmeldedaten für TTN

Mit folgenden Daten kann man sich beim TTN-Account unseres Teams anmelden, Einstellungen vornehmen und empfangene Sensordaten einsehen und Aktoren steuern:

THETHINGSNETWORK.ORG (Legacy V2 Console)
User name: htwgardenproject
Email address: htwgardenss21@gmail.com Password: htwgarden2021

Technische Spezifikation - Smarte Gartenbewässerung

4.5 Testphase 1 - Senden und Empfangen von Daten über TTN

Bevor die Verbindung der TTN-Server mit der Anwendung, OpenSenseMap und Telegram erstellt wird, testen wir zunächst die Kommunikation über LoRaWan mit MQTT-Mosquito, MQTT.Fx und MQTT-Explorer.
Wenn die Daten von LoRa32 sicher erzeugt werden, verbinden wir LoRa32 mit dem TTN-Server. Bei der TTN-Cloud kann man Uplinks (Signal von Sensoren) lesen, und die Downlinks (Signal zur Sensoren) schicken. Wir testen das Emfpangen von Sensordaten und das Schicken von Daten zur Steuerung von Aktoren.
In | unserer | Testschaltung | werden | die | Daten | des | DHT22 | Temperatur- | und
Luftfeuchtigkeitssensors vom Lora32 erfasst. Dann werden die Daten weiter an TNN gesendet. Bei jedem Senden leuchtet die grüne LED. Zusätzlich kann ein Signal von TTN aus gesendet werden um die rote LED an- bzw. auszuschalten.
Bei unserem ersten Test stand uns ein Lora32 v1 zur Verfügung. Ein Bild dieser Schaltung ist in nachfolgender Abbildung zu sehen:


Abbildung 6: Aufbau der Schaltung für den Test der LoRaWan-Verbindung (Lora32 V1 ohn Oled)

Technische Spezifikation - Smarte Gartenbewässerung

Wenig später stand uns die neuere Version des TTGO Lora32 zur Verfügung: Lora32 OLED V2.1.6. Auf dem Display werden direkt die gemessenen Sensordaten angezeigt. So konnten wir prüfen, ob die Daten korrekt an TTN übertragen werden und gleiche Werte angezeigt werden.


Abbildung7: Aufbau der Schaltung für den Test der LoRaWan-Verbindung (Lora32 OLED V2.1.6)

In Gitlab → Software → Node-Lora32 → src → main.cpp ist der C++ Code zu finden, der auf

dem Lora32 installiert ist. Grundlegend gibt es eine Funktion zum Auslesen der Sensordaten des DHT22, zum Steuern von einer grünen und einer roten LED, zur Umwandlung der Daten in Byte mit dem Encoder, um sie versenden zu können und zum Senden der Daten über die Lora-Antenne.
Die Daten werden von einem TTN-Gateway empfangen und ins TTN-Netzwerk zu einem TTN-Server weitergeleitet. Mit dem Tool MQTT-Mosquitto oder MQTT-Explorer oder mit der Website von von TTN können wir auf die Daten in TNN zugreifen und die Sensordaten auslesen.

Technische Spezifikation - Smarte Gartenbewässerung

1. MQTT-Mosquito (als Client betrachtet)
Folgende Daten werden zur Verbindung über MQTT benötigt (um auf die Daten auf dem Daten TTN-Server zuzugreifen):
App ID on TTN: mygardenproject
Access key on TTN: ttn-account-v2.60jnFj-pF6rapK8BtiWsr2CQXM8TufQspWzjreeI2Zc

Folgende Befehle müssen in die Konsole eingegeben werden :
Active Mosquito service:
net start mosquitto
Subcribe our topic:
mosquitto_sub -h eu.thethings.network -p 1883 -d -u mygardenproject -P ttn-account-v2.60jnFj-pF6rapK8BtiWsr2CQXM8TufQspWzjreeI2Zc -t #

In nachfolgendem Bild sieht man die Ausgabe in der CMD ür MQTT-Mosquitto.


Abbildung 8: MQTT Mosquito


Technische Spezifikation - Smarte Gartenbewässerung

2. MQTT-Explorer (Client)
Alternative könen wir auch mit Hilfe von MQTT-Explorer die Daten auslesen. Hier kann man sich mit den selben Anmeldedaten ins System einloggen.

Abbildung 9: Einloggen bei MQTT-Explorer

Hier kann die Ausgabe im MQTT-Explorer gesehen werden:

Abbildung 10: Ausgabe der Sensordaten MQTT-Explorer

Technische Spezifikation - Smarte Gartenbewässerung

3. TTN-Website (Server + Client)
Die schönste und einfachste Möglichkeit, um die Daten auszulesen, ist das direkte Nutzen der Website von TTN.
Um die Daten dekodieren zu können, muss zuerst das Payload-Format auf der Website von TTN geschrieben werden, um die empfangenen Daten von Byte zurück in ein lesbares Format umzuwandeln.
In folgendem Bild ist die Funktion zum Dekodieren zu sehen:


Abbildung 11: Payload-Dekodier-Code

Technische Spezifikation - Smarte Gartenbewässerung

Dann können die Daten bei TTN gelesen werden:


Abbildung 12: Datenausgabe TNN

Technische Spezifikation - Smarte Gartenbewässerung

5. Spezifikation der Hardware

5.1 Einzelteile

Nachfolgend aufgelistete Komponenten wurden von uns gezielt herausgesucht. Wir haben auf die Kompatibilität zwischen den Teilen geachtet und wenn nötig auch passende Adapter besorgt.
Ein detaillierter Schaltplan und Bauplan für die Bewässerungsanalge folgt demnächst.

Auflistung aller elektronischen Komponenten:

Tabelle 4: Elektronische Komponenten

Name | Beschreibung | Anwendungen | Schnittstellen & Spannungsbelegung | Bild


LoRa32 Mikrocontrolle r | Mikrocontroller board, wie ESP32 + LoRaWAN-Ante nne | Entwicklerboard, Steuerung, Regelung, Berechnungen, Drahtlose Verbindung mit WLAN, Bluetooth, LoRaWAN | Eingang 5V(default) Eingang 3.3V(option) Ausgang 5V, 3.3V | https://www.makershop.de/plattformen/esp8266/ttgo-esp32-paxcounter-lora/


Coolty High Pressure Diaphragm Water Pump | Pumpe | Wasser pumpen | Betriebsspannung DC 12V 100PSI 4L/min | https://amzn.to/3zsKp1O
AZDelivery 4-relay module 5 V | Relais | Steuerung der Pumpe | Eingang 5V/3V Aussgang max 250V/10A AC, 30V/10A DC | https://amzn.to/3iHNncN

Technische Spezifikation - Smarte Gartenbewässerung


EXLECO 12 V NC G1/2 Inch Electro Solenoid Valve | Magnetventil | Schließen des Wasserdurchflusses nach der Pumpe | G 1/2“ Betriebsspannung DC 12 V | https://amzn.to/3goN8BY


G1/4 inch pressure sensor | Wasserdruck-sensor | Messung des Wasserdrucks | Betriebsspannung DC 5 V G 1/4" (muss durch Spannungsteiler mit Lora32 verbinden) | https://amzn.to/3iDe3vh


ARCELI YF-S201 1-30L/min Water Flow Meter | Durchfluss-sensor | Messung des Wasserdurchflusses | The lowest rated operating voltage: DC4.5 5V-24V. Maximum working current: 15mA (DC 5V) Working Voltage Range: DC 5~18V | https://amzn.to/3xmhiM0
Aukru Ultrasonic Module HC-SR04 | Ultraschall-sensor | Messung des Wasserstandes | Static Current(Max) :2mA ; Electrical Level Eingang:5V. ranging distance: 2cm~500 cm resolution: 0.3 cm | https://amzn.to/3gmvwGU

Technische Spezifikation - Smarte Gartenbewässerung


DHT22 Digital Temperature and Humidity Sensor AM2302 | Temperatur-sensor (optional) | Messung der Temperatur und Luftfeuchtigkeit | Betriebsspannung 3.3V | https://amzn.to/3xkpc8r


AZDelivery Soil Moisture Sensor Hygrometer Module V1.2 | Bodenfeuchtig-keitssensor | Messung der Bodenfeuchte | Eingang 5V Ausgang 3.3V | https://amzn.to/3pSUmkS

Zusätzlich werden noch ein Steckbrett und Kabel zur Verbindung der Komponenten eingesetzt.

Technische Spezifikation - Smarte Gartenbewässerung

Auflistung Bewässerungskomponenten:

Tabelle 5: Bewässerungskomponenten

Name | Beschreibung | Anwendungen | Schnittstellen & Spannungsbelegung | Bild


Flexible Tube TX | Verbindung Schlauch | Verbindung der Teile für den Wasserfluss | 13 mm x 3 mm (1/2 Inch), 5 m Long PVC Hose with Fabric | https://amzn.to/3xr0hjP
Homgif Garden Irrigation System, Micro Drip Irrigation Kit | Bewässerung Schlauch (Drip System) | Beförderung des Wassers nach Magnetventil zu den Beeten, Bewässerung der Pflanzen | 30 m Schlauch bis zu 35-40 m² bewässern | https://amzn.to/3xlwLvH


T-piece with external/intern al/external thread | Schlauchverbing dung Schlauch Wasserdrucksse nsor | Anschluss des Wasserdrucksensors an der Wasserleitung | Size: G ½” max. Druck: 16 bar | https://amzn.to/3iElBy3


Threading Adapter | Wasserdrucksen sor Adapter | Adapter um Wasserdrucksensor mit T-Stück zu verbiWden | NPT 1/2 Male to G 1/4 Female | https://koolance.com/threading-ada pter-npt-1-2-male-to-g-1-4-female-a dt-n12m-g14f

Technische Spezifikation - Smarte Gartenbewässerung


Gardena Tap Connector | Schlauchverbing dung Schlauch Ventil-Drip System | Verbindung nach dem Magnetventil mit dem Drip-System | 21mm bzw. 1/2 Zoll zum Gartenschlauch (Gardena-Anschluss) | https://amzn.to/3gx6jIK


Sourcing Map 3 x Brass Hose Connector | Schlauchverbind ung Sensor zum Schlauch | Verbindung der Komponenten mit dem Verbindungsschlauch | Size: 14mm spike x G1/2 socket; Total length: 35mm; Hex width: 23mm; Spike length: 23mm | https://amzn.to/3wkJpuK
BGS 8095-12x20 | Hose Clamps | Befestigung der Schläuche zu den Komponenten (festziehen) | 12 x 20 mm | 10 Pieces | https://amzn.to/3gwqlmL
Hose Clamps 2 | Hose Clamps | Befestigung der Schläuche zu den Komponenten (festziehen) (andere Größe) | 8x12 mm, Stainless Steel, 10 pcs. | https://amzn.to/3gBAw9B

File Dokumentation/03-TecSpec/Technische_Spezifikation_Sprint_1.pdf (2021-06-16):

Technische Spezifikation - Smarte Gartenbewässerung

# Technische Spezifikation

# Smarte Gartenbewässerung über LoRaWAN

Mitarbeiter und Autoren:

- Rami Hammouda
- Khac Hoa Le
- Jaro Machnow

Letzte Änderung: 16.06.2021

Version: 1.3

16.06.2021 | Seite 1 von 27

Technische Spezifikation - Smarte Gartenbewässerung

Inhaltsverzeichnis

1. Einleitung | 4
1.1 Überblick | 4
1.2 Definitionen und Abkürzungen | 4
1.3 Vorhandene Dokumente | 4
2. Prozessüberblick | 4
2.1 Realisierungsprozess | 5
2.2 Fachlicher Workflow | 7
2.3 Checkliste | 8
3. Systemarchitektur und Infrastruktur | 10
3.1 Systemarchitektur | 10
3.2 Beschreibung der Komponenten | 11
4. Technische Spezifikation der Software | 12
4.1 Überblick Komponenten | 12
4.2 Schnittstellen zwischen den Komponenten | 14
4.3 Technologiestack | 15
4.4 Anmeldedaten für TTN | 16
4.5 Testphase 1 - Senden und Empfangen von Daten über TTN | 17
5. Spezifikation der Hardware | 23
5.1 Einzelteile | 23

Technische Spezifikation - Smarte Gartenbewässerung

Versionshistorie

Version | Datum | Verantwortlich | Änderung
1.0 | 29.05.2021 | Jaro Machnow | Dokumenterstellung
1.1 | 06.06.2021 | Jaro, Hoa Le, Rami | Ergänzungen
1.2 | 15.06.2021 | Jaro, Hoa Le, Rami | Ergänzungen
1.3 | 16.06.2021 | Rami, Hoa, Jaro | Vervollständigung der Dokument

Technische Spezifikation - Smarte Gartenbewässerung

1. Einleitung
1.1 Überblick

Es wird eine smarte und möglichst preisgünstige und überwachte Bewässerung von Beeten per Netzwerksteuerung über das The-Things-Network (TTN) gebaut. Im Urban Garden kontrolliert ein Mikrocontroller entsprechend der über das Netzwerk gesendeten Nutzereingaben oder eines autonomen Workflows verschiedene Sensoren und Aktoren. Mit Hilfe einer LoRaWAN-Antenne werden die Daten der Sensoren vom Urban Garden aus in das Netzwerk gesendet und können auf einem entfernten Computer ausgelesen werden und als Visualisierung auf OpenSenseMap.org angesehen werden.

Zu den Mechanismen der autonomen Steuerung gehören vor allem das Abschalten des Wasserflusses im Falle eines Lecks und das eigenständige Starten der Bewässerung beim Erreichen einer bestimmten Bodenfeuchte.

Für alle eingebauten Komponenten und Funktionen gilt der Grundsatz, dass das System in Zukunft leicht modular erweitert werden kann.

1.2 Definitionen und Abkürzungen

LoRaWan -Long Range Wide Area Network TTN - The Things Network

1.3 Vorhandene Dokumente

Tabelle 1: Vohandene Dokumente

Dokument | Autor(en) | Datum
Lastenheft | Rami Hammouda, Khac Hoa Le, Jaro Machnow | 28.04.2021
Lastenheft + Kommentare | + Prof. Dr. Mohammad Abuosba | 30.04.2021
Anforderung-Email | Holger Martin | 10.04.2021
Pflichtenheft | Rami Hammouda, Khac Hoa Le, Jaro Machnow | 19.05.2021
Pflichtenheft + Kommentare | + Prof. Dr. Mohammad Abuosba | 25.05.2021

Technische Spezifikation - Smarte Gartenbewässerung

2. Prozessüberblick

2.1 Realisierungsprozess

Nachfolgend ist eine Darstellung aller Funktionen und deren Unterteilung im Projekt:


Abbildung 1: Übersicht über die Aufgabenstruktur

Für die Realisierung des Projektes ist es zuerst nötig, alle notwendigen Teile herauszusuchen und zu bestellen. Dann kann damit begonnen werden die Funktionsfähigkeit des Hauptziels des Projektes sicherzustellen: Das Senden und Empfangen von Daten vom Urban Garden über das LoRaWAN-Netzwerk. Danach können parallel die Nutzerschnittstellen mit TTN verbunden und programmiert werden und der Mikrocontroller mit den zugehörigen

Technische Spezifikation - Smarte Gartenbewässerung

Komponenten eingerichtet werden. Zum Schluss wird das gesamte Bewässerungssystem mit allen Komponenten zusammengebaut und im Urban Garden installiert.
Der Realisierungsprozess ist in folgendem Diagramm dargestellt:


Abbildung 2: Diagramm des Realisisierungsprozesses

Technische Spezifikation - Smarte Gartenbewässerung

2.2 Fachlicher Workflow

Nachfolgen ist das Diagramm des fachlichen Workflows zu sehen. Hier kann die Zusammenarbeit der Software und Hardware gesehen werden und der Ablauf bei Benutzung, Überwachung und Steuerung des Systems.


Abbildung 3: Fachlicher Workflow

Technische Spezifikation - Smarte Gartenbewässerung

2.3 Checkliste

Zur Strukturierung unserer Arbeit und um zu wissen, was schon gemacht wurde und was noch zu erledigen ist, haben wir folgende Checkliste erstellt. Die Checkliste beinhaltet aktuell nur Punkte, die mit der Software im Zusammenhang stehen (für den 1. Sprint).

Controlling Sensors, Actors:

Collect current ambient parameters (Temperatur sensor, Humidity sensor, Air pressure sensor.. )
Collect current water level in water tank (Ultrasound sensor)
Collect current water hose parameters (Water pressure sensor, Water flow sensor) Control Actors (Water pump, Magnetic valve)

On LoraWan Server:

Send collected sensor data to TTN Network
Operate with ABP Mode or OTAA Mode (prefer OTAA) Support float decode payload
Support int decode payload
Binding Server with opensensemap.org

Operate Actors:

Remote control actors manually
Actors operates itself automatically based on pre-configuration Auto Mode and Manual Mode should be selectable

Sensor Data Visualization:

Simple sensor data are visualizated by opensensemap
Complex sensor data will be visualizated by a self development UI

Technische Spezifikation - Smarte Gartenbewässerung

UI Development:

Create a UI to get all current information of system
Control actors through simple user-friendly UI like button, not on JSON UI (comply to requirement from Mr. Prof. Dr.-Ing. Abuosba )
Pre-configuration parameters should be changeable (e.g through input fields) (comply to suggestion from Mr. Holger Martin )

Options:

An UI on mobile for convenient monitoring Send Notification to user for alert

Technische Spezifikation - Smarte Gartenbewässerung

3. Systemarchitektur und Infrastruktur

3.1 Systemarchitektur


Abbildung 4: Komponentendiagramm

Technische Spezifikation - Smarte Gartenbewässerung

3.2 Beschreibung der Komponenten

Das | Komponentendiagramm | zeigt | die | verschiedenen | Schichten | unseres
Bewässerungssystems:
- Ganz oben sind die Komponenten, mit denen der Nutzer interagieren kann. Dazu gehören die Anwendung und die OpenSenseMap. Bei der Anwendung sieht der Nutzer das Dashboard, in dem Sensordaten angezeigt werden können und Aktoren per Knopfdruck aktiviert oder deaktiviert werden können. Zudem kann die autonome Steuerung aktiviert werden. Die OpenSenseMap zeigt eine Karte und die Sensordaten für den Standort des Urban Gardens.
- In der Mitte befinden sich Komponenten, die die obere Anwendungsschicht mit den Sensoren und Aktoren im Urban Garden verbinden. Dazu gehören das TheThingsNetwork und der Lora32-Mikrocontroller. Über diese beiden Daten kommen die Sensordaten zur Nutzeranwendung und die Nutzereingaben zu den Aktoren. Die Kommunikation bzw. Übertragung der Daten erfolgt hier über das LoRaWan-Netzwerk und über das Internet. Nähere Informationen sind dazu in Punkt
| 4.2 nachzulesen.
- Unten befinden sich die Komponenten, die direkt im Urban Garden agieren, also alle Sensoren und Akoren. Dazu gehören: Wasserdrucksensor, Wasserdurchflusssensor, Wasserstandsensor, Bodenfeuchtigkeitssensor, Pumpe und Magnetventil. Diese Komponenten sind mit Lora32 verbunden und werden dadurch überwacht und
| gesteuert.

Technische Spezifikation - Smarte Gartenbewässerung

4. Technische Spezifikation der Software

4.1 Überblick Komponenten


Abbildung 5: Komponentendiagramm Software

Technische Spezifikation - Smarte Gartenbewässerung

Beschreibung der Software-Komponenten:

Tabelle 2: Software-Komponenten

SW Komponente | Funktionen | Sprache/Typ
Anwendung (geplant) | -Daten empfangen und anzeigen - Daten auswerten - Daten senden - Alles wird in einem Dashboard angezeigt | JavaScript (Node Js)
Opensensemap (geplant) | -Anzeigen der Messdaten auf einer Karte | Website Service als Client
Telegram (geplant) | -Schnell und aktuell die Daten und den Status vom System abrufen | API Service als Client
Lora32 (Software) | -Sensorendaten abrufen - Aktoren steuern - Signal schicken/empfangen. | Programming language C++
TTN | -Zentraler Server für LoRaWAN - Schnittstelle zwischen LoRaWAN und Client. - Datenbank: Automatische Speicherung der Daten einer Woche | Website Server

Technische Spezifikation - Smarte Gartenbewässerung

4.2 Schnittstellen zwischen den Komponenten

Die Datenübermittlung zwischen dem LoRa32-Mikrocontroller und der Anwendung erfolgt in mehreren Schritten:
1. LoRa32 sendet die Daten an TTN-Gateways mit Hilfe der LoRaWan-Antenne.
2. Das Gateway schickt die Daten weiter ins Internet an die TTN-Cloud durch HTTP.
3. Die Anwendung ist mit der TTN-Cloud verbunden und erhält so die Daten.

Die TTN-Cloud dient dabei zugleich als Datenbank und speichert automatische die Daten einer Woche. Die Anwendung dient als grafische Benutzeroberfläche, die es dem Nutzer ermöglicht die Daten aus dem System auszulesen und das System fernzusteuern. Umgekehrt, also von der Anwendung zum LoRa32, funktioniert der Vorgang analog:
1. Der Nutzer gibt Daten in der Anwendung ein. Die Daten werden an die TTN-Cloud übermittelt.
2. Die TTN-Cloud übermittelt die Daten über HTTP an das TTN-Gateway
3. Mit Hilfe der LoRaWan-Antenne werden die Daten vom Gateway an den LoRa32-Mikrocontroller gesendet.
Die OpenSenseMap auch mit der TTN-Cloud verknüpft, um Daten anzuzeigen. Das funktioniert auf die gleiche Weise, wie bei der Anwendung. OpenSenseMap dient als weitere Benutzerschnittstelle.
Zudem wird Telegram benutzt, um eine schnelle und unkomplizierte Kommunikation des Nutzers mit dem System zu ermöglichen. Telegram ist direkt mit der Anwendung verknüpft.

Technische Spezifikation - Smarte Gartenbewässerung

4.3 Technologiestack

Folgender Technologiestack wird für die Erstellung der Software für die Kommunikatin über LoRaWan verwendet:

Tabelle 3: Technologiestack

Operation System: | -Windows 10/(Linux)
IDE: | -Visual Studio Code - Platform IO
Framework: | -Arduino
Abhängigkeiten: | -MCCI LoraWAN LMIC Library v3.3 - Adafruit Unified Sensor v1.1.4 - DHT sensor library v1.4.2
Protokolle: | -MQTT - HTTP
Drahtlose Verbindung/ Kommunikation: | - LoRaWAN (Long Range Wide Area Network)
Tools: | -MQTT Mosquito - MQTT Explorer
Server: | -TTN (thethingsnetwork)
UI Programmierung: | -JavaScript - NodeJS
Hardware Programmierung: | -C++
Hardware: | -Lora32 (TTGO)

Technische Spezifikation - Smarte Gartenbewässerung

4.4 Anmeldedaten für TTN

Mit folgenden Daten kann man sich beim TTN-Account unseres Teams anmelden, Einstellungen vornehmen und empfangene Sensordaten einsehen und Aktoren steuern:

THETHINGSNETWORK.ORG (Legacy V2 Console)
User name: htwgardenproject
Email address: htwgardenss21@gmail.com Password: htwgarden2021

Technische Spezifikation - Smarte Gartenbewässerung

4.5 Testphase 1 - Senden und Empfangen von Daten über TTN

Bevor die Verbindung der TTN-Server mit der Anwendung, OpenSenseMap und Telegram erstellt wird, testen wir zunächst die Kommunikation über LoRaWan mit MQTT-Mosquito, MQTT.Fx und MQTT-Explorer.
Wenn die Daten von LoRa32 sicher erzeugt werden, verbinden wir LoRa32 mit dem TTN-Server. Bei der TTN-Cloud kann man Uplinks (Signal von Sensoren) lesen, und die Downlinks (Signal zur Sensoren) schicken. Wir testen das Emfpangen von Sensordaten und das Schicken von Daten zur Steuerung von Aktoren.
In | unserer | Testschaltung | werden | die | Daten | des | DHT22 | Temperatur- | und
Luftfeuchtigkeitssensors vom Lora32 erfasst. Dann werden die Daten weiter an TNN gesendet. Bei jedem Senden leuchtet die grüne LED. Zusätzlich kann ein Signal von TTN aus gesendet werden um die rote LED an- bzw. auszuschalten.
Bei unserem ersten Test stand uns ein Lora32 v1 zur Verfügung. Ein Bild dieser Schaltung ist in nachfolgender Abbildung zu sehen:


Abbildung 6: Aufbau der Schaltung für den Test der LoRaWan-Verbindung (Lora32 V1 ohn Oled)

Technische Spezifikation - Smarte Gartenbewässerung

Wenig später stand uns die neuere Version des TTGO Lora32 zur Verfügung: Lora32 OLED V2.1.6. Auf dem Display werden direkt die gemessenen Sensordaten angezeigt. So konnten wir prüfen, ob die Daten korrekt an TTN übertragen werden und gleiche Werte angezeigt werden.


Abbildung7: Aufbau der Schaltung für den Test der LoRaWan-Verbindung (Lora32 OLED V2.1.6)

In Gitlab → Software → Node-Lora32 → src → main.cpp ist der C++ Code zu finden, der auf

dem Lora32 installiert ist. Grundlegend gibt es eine Funktion zum Auslesen der Sensordaten des DHT22, zum Steuern von einer grünen und einer roten LED, zur Umwandlung der Daten in Byte mit dem Encoder, um sie versenden zu können und zum Senden der Daten über die Lora-Antenne.
Die Daten werden von einem TTN-Gateway empfangen und ins TTN-Netzwerk zu einem TTN-Server weitergeleitet. Mit dem Tool MQTT-Mosquitto oder MQTT-Explorer oder mit der Website von von TTN können wir auf die Daten in TNN zugreifen und die Sensordaten auslesen.

Technische Spezifikation - Smarte Gartenbewässerung

1. MQTT-Mosquito (als Client betrachtet)
Folgende Daten werden zur Verbindung über MQTT benötigt (um auf die Daten auf dem Daten TTN-Server zuzugreifen):
App ID on TTN: mygardenproject
Access key on TTN: ttn-account-v2.60jnFj-pF6rapK8BtiWsr2CQXM8TufQspWzjreeI2Zc

Folgende Befehle müssen in die Konsole eingegeben werden :
Active Mosquito service:
net start mosquitto
Subcribe our topic:
mosquitto_sub -h eu.thethings.network -p 1883 -d -u mygardenproject -P ttn-account-v2.60jnFj-pF6rapK8BtiWsr2CQXM8TufQspWzjreeI2Zc -t #

In nachfolgendem Bild sieht man die Ausgabe in der CMD ür MQTT-Mosquitto.


Abbildung 8: MQTT Mosquito


Technische Spezifikation - Smarte Gartenbewässerung

2. MQTT-Explorer (Client)
Alternative könen wir auch mit Hilfe von MQTT-Explorer die Daten auslesen. Hier kann man sich mit den selben Anmeldedaten ins System einloggen.

Abbildung 9: Einloggen bei MQTT-Explorer

Hier kann die Ausgabe im MQTT-Explorer gesehen werden:

Abbildung 10: Ausgabe der Sensordaten MQTT-Explorer

Technische Spezifikation - Smarte Gartenbewässerung

3. TTN-Website (Server + Client)
Die schönste und einfachste Möglichkeit, um die Daten auszulesen, ist das direkte Nutzen der Website von TTN.
Um die Daten dekodieren zu können, muss zuerst das Payload-Format auf der Website von TTN geschrieben werden, um die empfangenen Daten von Byte zurück in ein lesbares Format umzuwandeln.
In folgendem Bild ist die Funktion zum Dekodieren zu sehen:


Abbildung 11: Payload-Dekodier-Code

Technische Spezifikation - Smarte Gartenbewässerung

Dann können die Daten bei TTN gelesen werden:


Abbildung 12: Datenausgabe TNN

Technische Spezifikation - Smarte Gartenbewässerung

5. Spezifikation der Hardware

5.1 Einzelteile

Nachfolgend aufgelistete Komponenten wurden von uns gezielt herausgesucht. Wir haben auf die Kompatibilität zwischen den Teilen geachtet und wenn nötig auch passende Adapter besorgt.
Ein detaillierter Schaltplan und Bauplan für die Bewässerungsanalge folgt demnächst.

Auflistung aller elektronischen Komponenten:

Tabelle 4: Elektronische Komponenten

Name | Beschreibung | Anwendungen | Schnittstellen & Spannungsbelegung | Bild


LoRa32 Mikrocontrolle r | Mikrocontroller board, wie ESP32 + LoRaWAN-Ante nne | Entwicklerboard, Steuerung, Regelung, Berechnungen, Drahtlose Verbindung mit WLAN, Bluetooth, LoRaWAN | Eingang 5V(default) Eingang 3.3V(option) Ausgang 5V, 3.3V | https://www.makershop.de/plattformen/esp8266/ttgo-esp32-paxcounter-lora/


Coolty High Pressure Diaphragm Water Pump | Pumpe | Wasser pumpen | Betriebsspannung DC 12V 100PSI 4L/min | https://amzn.to/3zsKp1O
AZDelivery 4-relay module 5 V | Relais | Steuerung der Pumpe | Eingang 5V/3V Aussgang max 250V/10A AC, 30V/10A DC | https://amzn.to/3iHNncN

Technische Spezifikation - Smarte Gartenbewässerung


EXLECO 12 V NC G1/2 Inch Electro Solenoid Valve | Magnetventil | Schließen des Wasserdurchflusses nach der Pumpe | G 1/2“ Betriebsspannung DC 12 V | https://amzn.to/3goN8BY


G1/4 inch pressure sensor | Wasserdruck-sensor | Messung des Wasserdrucks | Betriebsspannung DC 5 V G 1/4" (muss durch Spannungsteiler mit Lora32 verbinden) | https://amzn.to/3iDe3vh


ARCELI YF-S201 1-30L/min Water Flow Meter | Durchfluss-sensor | Messung des Wasserdurchflusses | The lowest rated operating voltage: DC4.5 5V-24V. Maximum working current: 15mA (DC 5V) Working Voltage Range: DC 5~18V | https://amzn.to/3xmhiM0
Aukru Ultrasonic Module HC-SR04 | Ultraschall-sensor | Messung des Wasserstandes | Static Current(Max) :2mA ; Electrical Level Eingang:5V. ranging distance: 2cm~500 cm resolution: 0.3 cm | https://amzn.to/3gmvwGU

Technische Spezifikation - Smarte Gartenbewässerung


DHT22 Digital Temperature and Humidity Sensor AM2302 | Temperatur-sensor (optional) | Messung der Temperatur und Luftfeuchtigkeit | Betriebsspannung 3.3V | https://amzn.to/3xkpc8r


AZDelivery Soil Moisture Sensor Hygrometer Module V1.2 | Bodenfeuchtig-keitssensor | Messung der Bodenfeuchte | Eingang 5V Ausgang 3.3V | https://amzn.to/3pSUmkS

Zusätzlich werden noch ein Steckbrett und Kabel zur Verbindung der Komponenten eingesetzt.

Technische Spezifikation - Smarte Gartenbewässerung

Auflistung Bewässerungskomponenten:

Tabelle 5: Bewässerungskomponenten

Name | Beschreibung | Anwendungen | Schnittstellen & Spannungsbelegung | Bild


Flexible Tube TX | Verbindung Schlauch | Verbindung der Teile für den Wasserfluss | 13 mm x 3 mm (1/2 Inch), 5 m Long PVC Hose with Fabric | https://amzn.to/3xr0hjP
Homgif Garden Irrigation System, Micro Drip Irrigation Kit | Bewässerung Schlauch (Drip System) | Beförderung des Wassers nach Magnetventil zu den Beeten, Bewässerung der Pflanzen | 30 m Schlauch bis zu 35-40 m² bewässern | https://amzn.to/3xlwLvH


T-piece with external/intern al/external thread | Schlauchverbing dung Schlauch Wasserdrucksse nsor | Anschluss des Wasserdrucksensors an der Wasserleitung | Size: G ½” max. Druck: 16 bar | https://amzn.to/3iElBy3


Threading Adapter | Wasserdrucksen sor Adapter | Adapter um Wasserdrucksensor mit T-Stück zu verbiWden | NPT 1/2 Male to G 1/4 Female | https://koolance.com/threading-ada pter-npt-1-2-male-to-g-1-4-female-a dt-n12m-g14f

Technische Spezifikation - Smarte Gartenbewässerung


Gardena Tap Connector | Schlauchverbing dung Schlauch Ventil-Drip System | Verbindung nach dem Magnetventil mit dem Drip-System | 21mm bzw. 1/2 Zoll zum Gartenschlauch (Gardena-Anschluss) | https://amzn.to/3gx6jIK


Sourcing Map 3 x Brass Hose Connector | Schlauchverbind ung Sensor zum Schlauch | Verbindung der Komponenten mit dem Verbindungsschlauch | Size: 14mm spike x G1/2 socket; Total length: 35mm; Hex width: 23mm; Spike length: 23mm | https://amzn.to/3wkJpuK
BGS 8095-12x20 | Hose Clamps | Befestigung der Schläuche zu den Komponenten (festziehen) | 12 x 20 mm | 10 Pieces | https://amzn.to/3gwqlmL
Hose Clamps 2 | Hose Clamps | Befestigung der Schläuche zu den Komponenten (festziehen) (andere Größe) | 8x12 mm, Stainless Steel, 10 pcs. | https://amzn.to/3gBAw9B

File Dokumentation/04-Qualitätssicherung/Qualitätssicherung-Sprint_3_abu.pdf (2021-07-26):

# Qualitätssicherung

# Smarte Gartenbewässerung über LoRaWAN

### Mitarbeiter und Autoren:

### - Rami Hammouda

### - Khac Hoa Le

### - Jaro Machnow

### Letzte Änderung: 21.07.2021

### Version: 1.4

Sehr gut.
kleine Anmerkungen siee unten.

## Wertung QS: 5 Punkte

Qualitätssicherung - Smarte Gartenbewässerung

## Inhaltsverzeichnis

1. Testfälle | 4
1.1 Daten an TNN Netzwerk senden | 4
1.2 Verschiedene Datentypen können versendet und verarbeitet werden | 4
1.3 Daten an Aktoren senden | 5
1.4 Auslesen der Daten mit dem MQTT-Explorer | 5
1.5 Verzögerungstest zum Steuern der Aktoren | 6
1.6 Sensordaten werden im User Interface angezeigt | 7
1.7 Aktoren können manuell über das User Interface gesteuert werden | 8
1.8 Autonome Steuerung funktioniert und kann aktiviert und deaktiviert werden | 9
1.9 Sensordaten können in der Opensensemap angezeigt werden | 10
1.10 Ultraschallsensor kann in der Halterung angebracht werden | 11
1.11 Temperatur und Luftfeuchte werden vom Sensor korrekt gemessen | 12
1.12 Status kann über Telegram angefragt werden | 13
1.13 Fehler werden erkannt und angezeigt | 14
1.14 Parameter der autonomen Steuerung können eingestellt werden | 15
1.15 Diagramme der Signalstärke werden angezeigt | 16
1.16 Zusammengebautes Gesamtsystem funktioniert wie erwartet | 17
2. Testprotokoll | 18
3. Anhang | 18
21.07.2021 | Seite 2 von 19

Qualitätssicherung - Smarte Gartenbewässerung

## Versionshistorie

Version | Datum | Verantwortlich | Änderung
1.0 | 29.05.2021 | Jaro Machnow | Dokumenterstellung
1.1 | 05.06.2021 | Rami Hammouda | Testfälle
1.2 | 16.06.2021 | Rami, Hoa, Jaro | Vervollständigung Testfälle Sprint 1
1.3 | 30.06.2021 | Rami, Hoa, Jaro | Testfälle Sprint 2
1.4 | 21.07.2021 | Rami, Hoa, Jaro | Testfälle Sprint 3

## Vorhandene Dokumente

Tabelle 1: Vorhandene Dokumente

Dokument | Autor(en) | Datum
Lastenheft | Rami Hammouda, Khac Hoa Le, Jaro Machnow | 28.04.2021
Lastenheft + Kommentare | + Prof. Dr. Mohammad Abuosba | 30.04.2021
Anforderung-Email | Holger Martin | 10.04.2021
Pflichtenheft | Rami Hammouda, Khac Hoa Le, Jaro Machnow | 19.05.2021
Pflichtenheft + Kommentare | + Prof. Dr. Mohammad Abuosba | 25.05.2021
Technische Spezifikation | Rami Hammouda, Khac Hoa Le, Jaro Machnow | 21.07.2021

Qualitätssicherung - Smarte Gartenbewässerung

## 1. Testfälle
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

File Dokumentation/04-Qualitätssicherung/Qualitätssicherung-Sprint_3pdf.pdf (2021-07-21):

# Qualitätssicherung

# Smarte Gartenbewässerung über LoRaWAN

### Mitarbeiter und Autoren:

### - Rami Hammouda

### - Khac Hoa Le

### - Jaro Machnow

### Letzte Änderung: 21.07.2021

### Version: 1.4

Qualitätssicherung - Smarte Gartenbewässerung

## Inhaltsverzeichnis
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

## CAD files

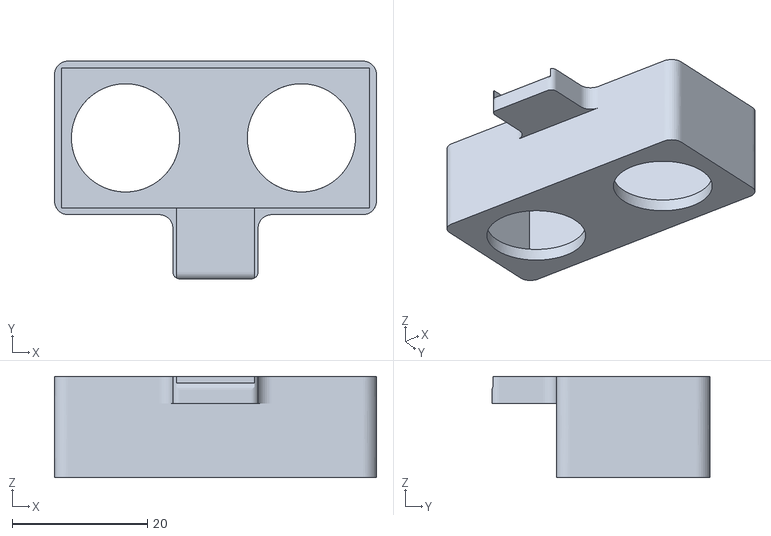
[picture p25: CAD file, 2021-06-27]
Hardware/Ultaschal Sensor Gehäuse/Ultaschal Sensor Gehäuse.stl
47.6 x 32.2 x 15.0

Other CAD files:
Hardware/Ultaschal Sensor Gehäuse/Ultaschal Sensor Gehäuse.ipt

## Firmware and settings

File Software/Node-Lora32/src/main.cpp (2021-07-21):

//Use Arduino framework on PlatformIO
#include <Arduino.h>
//For Lorawan
#include <lmic.h>
#include <hal/hal.h>
#include <SPI.h>
//For using ESP32 framework
#include <ESP.h>
//For Oled in Lora32 TTGO v2.1.6
#include <SSD1306.h>
//#include "SSD1306Wire.h"
#define OLED_I2C_ADDR 0x3C
#define OLED_RESET 16
#define OLED_SDA 21 //4  //21,22 for pin on Lora32 Oled v2.1.6
#define OLED_SCL 22 //15

//Created Class for wrapping sensor/actor
#include "UltrasonicSensor.h"
#include "PressureSensor.h"
#include "MoistureSensor.h"
#include "Actor.h"
#include "ActorGroup.h"

UltrasonicSensor ultrasonicSS;
PressureSensor pressureSS;
MoistureSensor moistureSS;
//boolean option ist for led-demonstration only, when we connect to Inverted relay
//default true: inverted relay is connected
//false: inverted relay ist not connected
Actor myPump(true), myVentil(true);
ActorGroup myActorSet;

//Define to check error of pump and ventil while operating
#define OPERATION_MODE
int notifyError = 100;

//Obsolete
//only for relay multiple mode- led notification only
//#define RELAY_INVERT
#ifdef RELAY_INVERT
bool mode = LOW;
#else
bool mode = HIGH;
#endif

//For BMESensor
#include <Wire.h>
#include <Adafruit_Sensor.h>
#include <Adafruit_BME280.h>
#define SEALEVELPRESSURE_HPA (1013.25)
Adafruit_BME280 bme; // I2C
SSD1306 display(OLED_I2C_ADDR, OLED_SDA, OLED_SCL);

//For Ultrasonic Sensor
//#include <NewPing.h>

#define TRIGGER_PIN 13   //34 (Important to pay attention, that pins from 34 to 39 are not able to be output )
#define ECHO_PIN 35      //35 (only be able to input)
#define MAX_DISTANCE 400 // Maximum sensor distance is rated at 400-500cm.
//NewPing sonar(TRIGGER_PIN, ECHO_PIN, MAX_DISTANCE);

//For Waterpressure Sensor
#define WATER_PRESSURE_PIN 36
//For WaterFlow Sensor
#define WATER_FLOW_PIN 34

//For Soil Moisture Sensor
#define MOISTURE_PIN 39

#define LEDPIN 3        //17
#define ACTOR_PUMPE 15  //23 //Led Red
#define ACTOR_VENTIL 12 //25  //Led Blue

float humi = 0, temC = 0, airPress = 0, altitude = 0, adcValue = 0, waterPress = 0;
int distanceToWaterSurface = 0, waterLeftInTank = 0; //(%) we will send waterleftIntank in % for better understanding
const int distanceToWaterAtBottomTank = 80;          //placeholder, accuray parameter is better;

//internal controlling
bool debugModeRq = true, manualModeRq = false, openVentilRq = false, openPumpRq = false, activeWateringRq = false;
//moisture level to turn on watering by Pertage = 95% = 0.95*1023 = 971; WaterVolume to Off by Litre (l)
int moistureOnPertg = 95, moistureOffPertg = 90, waterLvlOffPertg = 10, waterVolOffLit = 10; //200L, 10L only for testing

//variable for Waterflowsensor
int soilMoistureValue = 0, waterFlowSpeedValue = 0;
static unsigned int waterFlowVolValue = 0;
unsigned int flowMilliLitres;
unsigned long totalMilliLitres;
long currentMillis = 0, previousMillis = 0;
int intervalCheck = 1000;
//calibration factor
float calibrationFactor = 4.5;

volatile byte pulseCount;
byte pulse1Sec = 0;
float flowRate;
//Taskhandler in FreeRTOS for separate Core 0, to handle WaterflowSensor
TaskHandle_t Task1;

void IRAM_ATTR pulseCounter()
{
  pulseCount++;
}

//Structur for custom Lorawan Signal
typedef struct
{
  float temperature;
  float humidity;
  float airPressure;
  float waterPressure;
  int16_t waterLeft;
  int16_t soilMoisture;
  int16_t waterFlowSpeed;
  int16_t waterFlowVol;
  int16_t notifyCode;
  boolean openVentil;
  boolean openPump;
  boolean manualMode;

} sensorData;

#define PACKET_SIZE sizeof(sensorData)

typedef union
{
  sensorData sensor;
  byte LoRa_PacketBytes[PACKET_SIZE];
} LoRa_Packet;

LoRa_Packet mySensors;
char TTN_response[30];
int requestCodeFromServer;

//Device 2 on Server
// LoRaWAN NwkSKey, network session key
static const PROGMEM u1_t NWKSKEY[16] = {0xBF, 0x44, 0x04, 0x36, 0xB4, 0x9C, 0x5A, 0x85, 0x07, 0x5B, 0xEE, 0x33, 0xB6, 0x0A, 0x52, 0xCC};
// LoRaWAN AppSKey, application session key
static const u1_t PROGMEM APPSKEY[16] = {0xD4, 0xD6, 0x5D, 0xB5, 0x3C, 0xC0, 0x12, 0x75, 0xE3, 0x8E, 0x72, 0xD2, 0x90, 0x69, 0x3B, 0xD5};
static const u4_t DEVADDR = 0x260139A5;

void os_getArtEui(u1_t *buf) {}
void os_getDevEui(u1_t *buf) {}
void os_getDevKey(u1_t *buf) {}

// payload to send to TTN gateway
//static uint8_t payload[7];
static osjob_t sendjob;

// Schedule TX every this many seconds (might become longer due to duty
// cycle limitations).
static unsigned TX_INTERVAL = 5;
int short_interval = 5, long_interval = 58; //60s
// Pin mapping
const lmic_pinmap lmic_pins = {
    .nss = 18,
    .rxtx = LMIC_UNUSED_PIN,
    .rst = 14,
    .dio = {26, 33, 32} // Pins for the Heltec ESP32 Lora board/ TTGO Lora32 with 3D metal antenna
};

//Re-implement map with float, incase we need to use float as input with small range
float mapWithFloat(float x, float in_min, float in_max, float out_min, float out_max)
{
  const float dividend = out_max - out_min;
  const float divisor = in_max - in_min;
  const float delta = x - in_min;
  if (divisor == 0)
  {
    log_e("Invalid map input range, min == max");
    return -1;
  }
  return (delta * dividend + (divisor / 2)) / divisor + out_min;
}

/// Main function to calculate waterflow sensor
void processWaterFlowSensor(void *pvParameters)
{
  for (;;)
  {
    currentMillis = millis();
    if (currentMillis - previousMillis > intervalCheck)
    {

      pulse1Sec = pulseCount;
      pulseCount = 0;
      flowRate = ((1000.0 / (millis() - previousMillis)) * pulse1Sec) / calibrationFactor;
      previousMillis = millis();
      flowMilliLitres = (flowRate / 60) * 1000;
      totalMilliLitres += flowMilliLitres;

      waterFlowSpeedValue = (int)flowRate;
      waterFlowVolValue = totalMilliLitres / 1000;
    }

    vTaskDelay(5);
  }
}

void turnOnVentil()
{
  myActorSet.turnOnPassiveActors();
  openVentilRq = true;
};
void turnOffVentil()
{
  myActorSet.turnOffPassiveActors();
  openVentilRq = false;
}
void turnOnPump()
{
  myActorSet.turnOnActiveActors();
  openPumpRq = true;
};
void turnOffPump()
{
  myActorSet.turnOffActiveActors();
  openPumpRq = false;
}
//delay 2s to avoid dynamic water pressure detroying system
void turnOnWatering()
{
  myActorSet.turnOnAllActors();
  openVentilRq = true;
  openPumpRq = true;
}
void turnOffWatering()
{
  myActorSet.turnOffAllActors();
  openVentilRq = false;
  openPumpRq = false;
}
void turnOnDebugMode()
{
  debugModeRq = true;
  TX_INTERVAL = short_interval;
  Serial.println("Set update interval time = " + String(short_interval) + "s");
}
void turnOffDebugMode()
{
  debugModeRq = false;
  TX_INTERVAL = long_interval;
  Serial.println("Set update interval time = " + String((float)long_interval / 60) + "min");
}
void rebootSystem(int rebootTime = 5)
{
  for (int i = rebootTime; i >= 0; --i)
  {
    Serial.println("System will be reboot in " + String(i) + " s");
    delay(1000);
  }
  Serial.println("Rebooting...");
  ESP.restart();
}
String boolToString(bool value) { return value ? "TRUE" : "FALSE"; }
void HandlerDownlinksFromServer(lmic_t &lmic)
{
  int i = 0;
  // data received in rx slot after tx
  Serial.print(F("Data Received: "));
  Serial.write(lmic.frame + lmic.dataBeg, lmic.dataLen);
  Serial.println();

  //display.drawString (0, 20, "Received DATA.");
  for (i = 0; i < lmic.dataLen; i++)
    TTN_response[i] = lmic.frame[lmic.dataBeg + i];

  TTN_response[i] = 0;
  char *pNext;
  //requestCodeFromServer = (int) (TTN_response);
  requestCodeFromServer = strtol(TTN_response, &pNext, 10);
  display.drawString(0, 20, "Request Code " + String(requestCodeFromServer));
  Serial.println(String(requestCodeFromServer));

  //Request Code:
  //11001: TurnOnWatering on Manual Mode
  //10001: TurnOffWatering on Manual Mode
  //210xx: Moisture level to active watering from above xx% on Auto Mode
  //200xx: Moisture level to turn off watering from below xx% and below on Auto Mode
  //300xx: Water level to turn off watering from below xx% on Auto Mode
  //40xxx: Water Volume to turn off watering from above xxx% automatically
  //71001: Turn on Pumpe (for testing only)
  //70001: Turn off Pumpe (for testing only)
  //71002: Turn on Ventils (for testing only)
  //70002: Turn off Ventils (for testing only)
  //81001: Turn on Manual Mode
  //80001: Turn off Manual Mode (change to AutoMode)
  //91001: Turn on Debug Mode (TX_INTERVAL will be shorter): actually 9s update change on Server
  //90001: Turn off Debug Mode (TX_INTERVAL will be longer): 30min to update to Server

  switch (requestCodeFromServer)
  {
  case 11001:
    if (manualModeRq)
      turnOnWatering();
    break; //31 31 30 30 31 in Hexa
  case 10001:
    if (manualModeRq)
      turnOffWatering();
    break; //31 30 30 30 31
  case 71001:
    turnOnPump();
    break; //37 31 30 30 31
  case 70001:
    turnOffPump();
    break; //37 30 30 30 31
  case 71002:
    turnOnVentil();
    break; //37 31 30 30 32
  case 70002:
    turnOffVentil();
    break; //37 30 30 30 32
  case 81001:
    manualModeRq = true;
    break; //38 31 30 30 31
  case 80001:
    manualModeRq = false;
    break; //38 30 30 30 31
  case 91001:
    turnOnDebugMode();
    break;
  case 90001:
    turnOffDebugMode();
    break;
  case 99999:
    rebootSystem();
    break; //39 39 39 39 39
  default:
    if (requestCodeFromServer >= 21000 && requestCodeFromServer <= 21100)
    {
      moistureOnPertg = requestCodeFromServer == 21100 ? 100 : requestCodeFromServer % 100;
      Serial.println("Set Moisture On Pertage: " + String(moistureOnPertg) + "%");
    }
    if (requestCodeFromServer >= 20000 && requestCodeFromServer <= 20100)
    {
      moistureOffPertg = requestCodeFromServer == 20100 ? 100 : requestCodeFromServer % 100;
      Serial.println("Set Moisture Off Pertage: " + String(moistureOffPertg) + "%");
    }
    if (requestCodeFromServer >= 30000 && requestCodeFromServer <= 30100)
    {
      waterLvlOffPertg = requestCodeFromServer == 30100 ? 100 : requestCodeFromServer % 100;
      Serial.println("Set Water level Off Pertage: " + String(waterLvlOffPertg) + "%");
    }
    if (requestCodeFromServer >= 40000 && requestCodeFromServer <= 40200)
    {
      waterVolOffLit = requestCodeFromServer == 40200 ? 200 : requestCodeFromServer % 200;
      Serial.println("Set Water flow Volume Off Listre: " + String(waterVolOffLit) + "L");
    }
  }
}

int errorChecking()
{
  if (openVentilRq && openPumpRq && waterFlowSpeedValue < 1)
  {
    //This is only simulation testing.
    //Because these below values need to be suitable to pratical operation
    //These values might need to be changed
    if (waterPress > 5.5)
    {
      Serial.println("Got stuck!!! May be ventil defect or stuck in Hose");
      return 101;
    }
    if (waterPress < 1.02)
    {
      Serial.println("Pump defect");
      return 102;
    }
    return 100;
  }
  return 100;
}
//Error Handler function
//It checks error Code, current status and give a corresponding handle
void errorHandler()
{
  Serial.println("System Error checking");
  if (errorChecking() == 100)
    return;
  Serial.println("Defect detected, All Actors must be shutdowned now");
  //myActorSet.turnOffAllActors();
  turnOffWatering();
  manualModeRq = true;
}
//With old version of LMIC Library we can only add inline function into provided function of LMIC
//With new version of LMIC now we can add normal functions
//And now functions in main loop can also work well (but need to pay attention to avoid conflict between function in main loop vs scheduled transmission or block transsmisstion)
inline void GetAndUpdateSensorData()
{
  temC = bme.readTemperature() - 1.5; //calibration
  humi = bme.readHumidity();

  if (isnan(humi) || isnan(temC))
  {
    Serial.println(F("Failed to read from bme sensor!"));
    return;
  }
  airPress = bme.readPressure() / 100.0F;
  altitude = bme.readAltitude(SEALEVELPRESSURE_HPA);

  //Ultrasonic sensor:
  distanceToWaterSurface = (int)ultrasonicSS.getDistance_cm();
  Serial.println("actually mesuared distance " + String(distanceToWaterSurface));
  //Remove outliner of Value
  distanceToWaterSurface = distanceToWaterSurface > distanceToWaterAtBottomTank ? distanceToWaterAtBottomTank : distanceToWaterSurface;
  Serial.println("distance after fix " + String(distanceToWaterSurface));
  //water lef in tank wird be calculated in percentage
  waterLeftInTank = (float)(distanceToWaterAtBottomTank - distanceToWaterSurface) / distanceToWaterAtBottomTank * 100;
  Serial.printf("Temp: %.2f °C, Humidity: %.2f %%, Air Pressure: %.2f hPa, Altitude: %.2f m\n", temC, humi, airPress, altitude);
  Serial.println("Water Level: " + String(waterLeftInTank) + " %");

  //Get Waterpressure Data:
  waterPress = pressureSS.getPressure_bar();
  Serial.println("Water Pressure: " + String(waterPress) + " Bar");

  //Get Waterflow data

  //Get soil Moisture data
  soilMoistureValue = (float)moistureSS.getMoisture_percent();
  if (isnan(soilMoistureValue))
  {
    Serial.println(F("Failed to read soil Moisture value from Sensor!"));
    return;
  }

  Serial.println("Moisture Value: " + String(soilMoistureValue) + "% - Flow rate: " + String(int(waterFlowSpeedValue)) + "L/min \t Total Liquid Quantity: " + String(waterFlowVolValue) + "L\n");

#ifdef OPERATION_MODE
  notifyError = errorChecking();
#endif

  //Packing data to send
  mySensors.sensor.temperature = temC;
  mySensors.sensor.humidity = humi;
  mySensors.sensor.airPressure = airPress / 1000;
  mySensors.sensor.waterPressure = waterPress;
  mySensors.sensor.waterLeft = waterLeftInTank;
  mySensors.sensor.soilMoisture = soilMoistureValue;
  mySensors.sensor.waterFlowSpeed = waterFlowSpeedValue;
  mySensors.sensor.waterFlowVol = waterFlowVolValue;
  mySensors.sensor.notifyCode = (int16_t)notifyError;
  mySensors.sensor.openVentil = openVentilRq;
  mySensors.sensor.openPump = openPumpRq;
  mySensors.sensor.manualMode = manualModeRq;

  digitalWrite(LEDPIN, HIGH);
}

/**
 * Main function to evaluate various parameter to give final decision for controlling watering system
 */
void operateSystemAutomatically()
{
  if (manualModeRq || (errorChecking() != 100))
    return;

  bool moistureOn, moistureOff, waterLvlOff, waterVolOff, finalDecision;
  moistureOn = soilMoistureValue > moistureOnPertg;
  moistureOff = soilMoistureValue < moistureOffPertg;
  waterLvlOff = waterLeftInTank < waterLvlOffPertg;
  waterVolOff = waterFlowVolValue > waterVolOffLit;

  Serial.println("Condition check:\nPass Check Moisture On: " + boolToString(moistureOn) + "\nPass Check Moisture Off: " + boolToString(!moistureOff) +
                 "\nPass Check Waterlevel Off: " + boolToString(!waterLvlOff) + "\nPass Check WaterVolume Off: " + boolToString(!waterVolOff));
  finalDecision = moistureOn && !moistureOff && !waterLvlOff && !waterVolOff;

  Serial.println("Final Decision - Turn On Watering: " + boolToString(finalDecision) + "\n\n");
  if (finalDecision)
  {
    delay(500);
    turnOnWatering();
  }
  else
  {
    turnOffWatering();
    //if (waterFlowVolValue > 0)
    //ESP.restart();
  }
}

void displayAllInforOnOled()
{
  //oled:
  display.drawString(0, 10, String(millis()));
  display.drawString(0, 30, "Te " + String(temC) + "°C");
  display.drawString(70, 30, "Hu " + String(humi) + "%");
  display.drawString(0, 40, "A.P " + String(airPress / 1000) + "Bar");
  display.drawString(70, 40, "W.P " + String(waterPress) + "Bar");
  display.drawString(0, 50, "W.L " + String(waterLeftInTank) + "%");
  display.drawString(45, 50, "M " + String(soilMoistureValue) + "%");
  display.drawString(75, 50, " W.Vl  " + String(waterFlowVolValue) + "L");
  display.display();
}

void do_send(osjob_t *j)
{
  // Check if there is not a current TX/RX job running
  if (LMIC.opmode & OP_TXRXPEND)
  {
    Serial.println(F("OP_TXRXPEND, not sending"));
  }
  else
  {
    // read the sensorvalue
    GetAndUpdateSensorData();
    operateSystemAutomatically();
    errorHandler();

    LMIC_setTxData2(16, mySensors.LoRa_PacketBytes, sizeof(mySensors.LoRa_PacketBytes), 0);
  }
  // Next TX is scheduled after TX_COMPLETE event.
}

void onEvent(ev_t ev)
{
  Serial.print(os_getTime());
  Serial.print(": ");
  switch (ev)
  {
  case EV_SCAN_TIMEOUT:
    Serial.println(F("EV_SCAN_TIMEOUT"));
    break;
  case EV_BEACON_FOUND:
    Serial.println(F("EV_BEACON_FOUND"));
    break;
  case EV_BEACON_MISSED:
    Serial.println(F("EV_BEACON_MISSED"));
    break;
  case EV_BEACON_TRACKED:
    Serial.println(F("EV_BEACON_TRACKED"));
    break;
  case EV_JOINING:
    Serial.println(F("EV_JOINING"));
    break;
  case EV_JOINED:
    Serial.println(F("EV_JOINED"));
    break;
  case EV_JOIN_FAILED:
    Serial.println(F("EV_JOIN_FAILED"));
    break;
  case EV_REJOIN_FAILED:
    Serial.println(F("EV_REJOIN_FAILED"));
    break;
  case EV_TXCOMPLETE:
    //Oled
    display.clear();
    display.drawString(0, 0, "EV_TXCOMPLETE event!");

    Serial.println(F("EV_TXCOMPLETE (includes waiting for RX windows)"));
    if (LMIC.txrxFlags & TXRX_ACK)
      Serial.println(F("Received ack"));
    if (LMIC.dataLen)
    {
      Serial.println("Received " + String(LMIC.dataLen) + " bytes of payload");
      HandlerDownlinksFromServer(LMIC);
    }
    // Schedule next transmission
    os_setTimedCallback(&sendjob, os_getTime() + sec2osticks(TX_INTERVAL), do_send);
    //Turn led:
    digitalWrite(LEDPIN, LOW);
    displayAllInforOnOled();
    break;
  case EV_LOST_TSYNC:
    Serial.println(F("EV_LOST_TSYNC"));
    break;
  case EV_RESET:
    Serial.println(F("EV_RESET"));
    break;
  case EV_RXCOMPLETE:
    // data received in ping slot
    Serial.println(F("EV_RXCOMPLETE"));
    break;
  case EV_LINK_DEAD:
    Serial.println(F("EV_LINK_DEAD"));
    break;
  case EV_LINK_ALIVE:
    Serial.println(F("EV_LINK_ALIVE"));
    break;
  case EV_TXSTART:
    Serial.println(F("EV_TXSTART"));
    break;
  case EV_TXCANCELED:
    Serial.println(F("EV_TXCANCELED"));
    break;
  case EV_RXSTART:
    /* do not print anything -- it wrecks timing */
    break;
  case EV_JOIN_TXCOMPLETE:
    Serial.println(F("EV_JOIN_TXCOMPLETE: no JoinAccept"));
    break;
  default:
    Serial.print(F("Unknown event: "));
    Serial.println((unsigned)ev);
    break;
  }
}

void setup()
{
  delay(1500);
  while (!Serial)
    ;
  Serial.begin(9600);
  delay(100);
  Serial.println(F("Starting"));

  //start bme sensor:
  if (!bme.begin(0x76))
  {
    Serial.println("Could not find a valid BME280 sensor, check wiring!");
    while (1)
      delay(10);
  }
  pinMode(LEDPIN, OUTPUT);
  //pinMode(ACTOR_VENTIL, OUTPUT);
  //pinMode(ACTOR_PUMPE, OUTPUT);
  pinMode(TRIGGER_PIN, OUTPUT);
  pinMode(ECHO_PIN, INPUT);
  pinMode(WATER_FLOW_PIN, INPUT_PULLUP);
  pinMode(MOISTURE_PIN, INPUT);
  //use default same SDA,SCL of I2C Pins for BME Sensor

  //Custom classes:
  ultrasonicSS.set_trig_echo(TRIGGER_PIN, ECHO_PIN);
  pressureSS.setInputPin(WATER_PRESSURE_PIN);
  moistureSS.setInputPin(MOISTURE_PIN);

  myPump.setOutputPin(ACTOR_PUMPE);
  myVentil.setOutputPin(ACTOR_VENTIL);

  myActorSet.addActiveActor(myPump);
  myActorSet.addPassiveActor(myVentil);

  pulseCount = 0;
  flowRate = 0.0;
  flowMilliLitres = 0;
  totalMilliLitres = 0;
  previousMillis = 0;

  attachInterrupt(digitalPinToInterrupt(WATER_FLOW_PIN), pulseCounter, FALLING);

  xTaskCreatePinnedToCore(
      processWaterFlowSensor, /* Task function. */
      "Task1",                /* name of task. */
      5000,                   /* Stack size of task */
      NULL,                   /* parameter of the task */
      1,                      /* priority of the task */
      &Task1,                 /* Task handle to keep track of created task */
      0);                     /* pin task to core 0 */
  delay(500);

  // reset the OLED
  pinMode(OLED_RESET, OUTPUT);
  digitalWrite(OLED_RESET, LOW);
  delay(50);
  digitalWrite(OLED_RESET, HIGH);

  display.init();
  display.flipScreenVertically();
  display.setFont(ArialMT_Plain_10);

  display.setTextAlignment(TEXT_ALIGN_LEFT);

  display.drawString(0, 0, "Init!");
  display.display();

  // LMIC init
  os_init();
  // Reset the MAC state. Session and pending data transfers will be discarded.
  LMIC_reset();

  // Copy static session parameters to a temporary buffer here
  uint8_t appskey[sizeof(APPSKEY)];
  uint8_t nwkskey[sizeof(NWKSKEY)];
  memcpy_P(appskey, APPSKEY, sizeof(APPSKEY));
  memcpy_P(nwkskey, NWKSKEY, sizeof(NWKSKEY));
  LMIC_setSession(0x13, DEVADDR, nwkskey, appskey);

  // We'll disable all 72 channels used by TTN
  for (int c = 0; c < 72; c++)
  {
    LMIC_disableChannel(c);
  }

  LMIC_setupChannel(0, 868100000, DR_RANGE_MAP(DR_SF12, DR_SF7), BAND_CENTI);  // g-band
  LMIC_setupChannel(1, 868300000, DR_RANGE_MAP(DR_SF12, DR_SF7B), BAND_CENTI); // g-band
  LMIC_setupChannel(2, 868500000, DR_RANGE_MAP(DR_SF12, DR_SF7), BAND_CENTI);  // g-band
  LMIC_setupChannel(3, 867100000, DR_RANGE_MAP(DR_SF12, DR_SF7), BAND_CENTI);  // g-band
  LMIC_setupChannel(4, 867300000, DR_RANGE_MAP(DR_SF12, DR_SF7), BAND_CENTI);  // g-band
  LMIC_setupChannel(5, 867500000, DR_RANGE_MAP(DR_SF12, DR_SF7), BAND_CENTI);  // g-band
  LMIC_setupChannel(6, 867700000, DR_RANGE_MAP(DR_SF12, DR_SF7), BAND_CENTI);  // g-band
  LMIC_setupChannel(7, 867900000, DR_RANGE_MAP(DR_SF12, DR_SF7), BAND_CENTI);  // g-band
  LMIC_setupChannel(8, 868800000, DR_RANGE_MAP(DR_FSK, DR_FSK), BAND_MILLI);   // g2-band

  // Disable link check validation
  LMIC_setLinkCheckMode(0);

  // TTN uses SF9 for its RX2 window.
  LMIC.dn2Dr = DR_SF7;

  // Set data rate and transmit power for uplink
  LMIC_setDrTxpow(DR_SF7, 14);

  // Start job
  do_send(&sendjob);
}

void loop()
{
  os_runloop_once();
}

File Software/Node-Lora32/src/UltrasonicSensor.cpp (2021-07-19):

#include "UltrasonicSensor.h"

bool UltrasonicSensor::set_trig_echo(uint8_t trig, uint8_t echo) 
{
	set_trig(trig);
	setInputPin(echo);
	return true; 
}

bool UltrasonicSensor::set_trig(uint8_t trig)
{
	triggerPin = trig;
	pinMode(triggerPin, OUTPUT); // Sets the outputPin as an OUTPUT
	return true;
}

int UltrasonicSensor::getDistance_cm()
{
	// Clears the trigPin condition
  	digitalWrite(triggerPin, LOW);
  	delayMicroseconds(2);
  	// Sets the trigPin HIGH (ACTIVE) for 10 microseconds
	digitalWrite(triggerPin, HIGH);
	delayMicroseconds(10);
	digitalWrite(triggerPin, LOW);
	// Reads the echoPin, returns the sound wave travel time in microseconds
	double duration = pulseIn(inputPin, HIGH);
	// Calculating the distance
	double distance = duration * 0.034 / 2; // Speed of sound wave divided by 2 (go and back)
	// Displays the distance on the Serial Monitor

	return (int)distance;

}

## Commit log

2021-06-06 Update README to current status
2021-06-07 - Connect and send multiple sensor data to TTN Server
2021-06-27 Ultaschal Sensor Gehäuse
    [Ultaschal Sensor Gehäuse.ipt, Ultaschal Sensor Gehäuse.stl]
2021-06-30 Update Infor to current Status.md
2021-06-30 - Change board to LoraV2.1 with Oled - Add Oled Driver - Update LMIC library for better stable signal
